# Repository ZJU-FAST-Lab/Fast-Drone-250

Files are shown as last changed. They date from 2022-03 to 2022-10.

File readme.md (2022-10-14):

<font size=6> **从零制作自主空中机器人** </font>

本文档是视频教程[从零制作自主空中机器人](https://www.bilibili.com/video/BV1WZ4y167me?p=1)的配套文档,github链接为https://github.com/ZJU-FAST-Lab/Fast-Drone-250

<font color="#dd0000">安全事项</font>

四旋翼无人机具有较高的安全风险，请同学们严格遵守安全规范，不要在有人的室内或室外进行试验，对自己和他人的安全负责，本实验室完全免责。

- [第一章：课程介绍](#第一章课程介绍)
- [第二章：动力套焊接](#第二章动力套焊接)
- [第三章：飞控的安装与接线](#第三章飞控的安装与接线)
- [第四章：飞控设置与试飞](#第四章飞控设置与试飞)
- [第五章：机载电脑与传感器的安装](#第五章机载电脑与传感器的安装)
- [第六章：Ubuntu20.04的安装](#第六章ubuntu2004的安装)
- [第七章：机载电脑的环境配置](#第七章机载电脑的环境配置)
- [第八章：常用实验与调试软件的安装与使用](#第八章常用实验与调试软件的安装与使用)
- [第九章：Ego-Planner代码框架与参数介绍](#第九章ego-planner代码框架与参数介绍)
- [第十章：VINS的参数设置与外参标定](#第十章vins的参数设置与外参标定)
- [第十一章：Ego-Planner的实验](#第十一章ego-planner的实验)
- [Q&A 常见问题及解答](#qa-常见问题及解答)

## 第一章：课程介绍
  本次课程是一套面向对自主空中机器人感兴趣的学生、爱好者、相关从业人员的免费课程，包含了从硬件组装、机载电脑环境设置、代码部署、实机实验等全套详细流程，带你从0开始，组装属于自己的自主无人机，并让它可以在未知的环境中自由避障穿行。本次课程所涉及的所有代码、硬件设计全部开源，<font color="#dd0000">严禁商用与转载，版权与最终解释权由浙江大学FASTLAB实验室所有。</font>
  本次课程的重心主要落在自主空中机器人的搭建、代码部署及调试上，关于自主空中机器人的一些理论基础，例如动力学模型，路径搜索，轨迹规划，地图构建等内容，高飞老师在深蓝学院有非常详尽而深入浅出的[课程](https://www.shenlanxueyuan.com/course/385?source=1)，本次课程就不再赘述。

## 第二章：动力套焊接
  机器人本体相关配件及焊接用工具详见[purchase_list.xlsx](purchase_list.xlsx),对硬件选型有相关疑问请看 番外一：硬件选型
## 第三章：飞控的安装与接线
* 一定要注意电调信号线顺序！！！
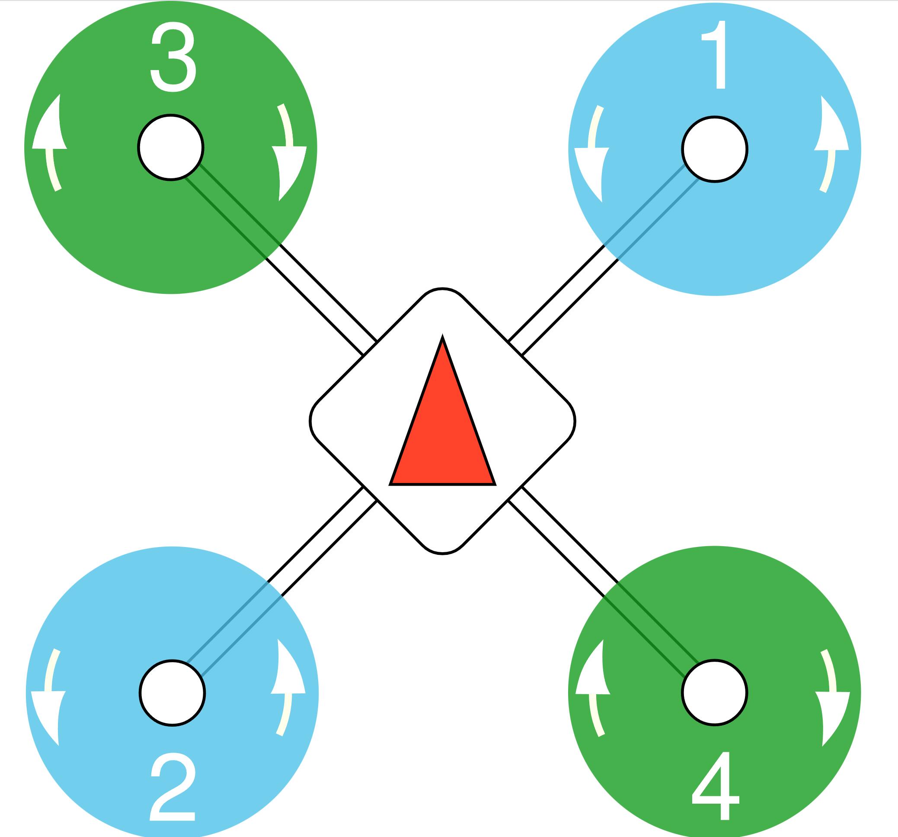
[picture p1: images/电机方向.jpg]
电机方向
  
* 飞控箭头与机头同向为正向，任意方向旋转90°的倍数也可以，后续可以在飞控设置内调整，推荐和视频内相同朝向摆放。
* <font color="#dd0000">强烈推荐使用硅胶杜邦线，常规杜邦线线材过硬，容易出现接触不良。</font>
* 5V稳压模块注意贴黑胶带绝缘，周围注意贴一圈厚的海绵胶带来防止飞机降落时损坏5V模块，也可以考虑把5V模块用扎带扎在机臂旁边
* 使用V5+飞控或其他把模拟和数字输出分开的飞控（特点是输出口标号为A1~A4 M1~M4），如果要用Dshot协议，请插在A口上

## 第四章：飞控设置与试飞

* 请烧录本git项目下的`/firmware/px4_fmu-v5_default.px4`固件，这个固件是官方1.11.0版本固件编译而来，如有需要可以自行编译。实测1.13版本固件存在BUG，不建议使用，更老的固件版本未经测试。

* 在飞控的sd卡的根目录下创建`/etc/extras.txt`，写入

  ```
  mavlink stream -d /dev/ttyACM0 -s ATTITUDE_QUATERNION -r 200
  mavlink stream -d /dev/ttyACM0 -s HIGHRES_IMU -r 200
  ```
  
  以提高imu发布频率
  
* 修改机架类型为 `Generic 250 Racer`，代指250mm轴距机型。如果是其他尺寸的机架，请根据实际轴距选择机架类型

* 修改`dshot_config`为dshot600

* 修改`CBRK_SUPPLY_CHK`为894281 *执行这步跳过了电源检查，因此左侧栏的电池设置部分就算是红的也没关系*

* 修改`CBRK_USB_CHK`为197848

* 修改`CBRK_IO_SAFETY`为22027

* 修改`SER_TEL1_BAUD`为921600

* 修改`SYS_USE_IO`为0（搜索不到则不用管）

* 上电前请先用万用表通断档检测电源正负焊点是否短接，强烈建议第一次上电前先接一个[短路保护器](https://item.taobao.com/item.htm?spm=a230r.1.14.6.72b83b20uNbZk7&id=656973651729&ns=1&abbucket=19#detail)

* <font color="#dd0000">检测电机转向前确保没有安装螺旋桨！！！！</font>

* 修改电机转向：进入mavlink控制台

  ```
  dshot reverse -m 1
  dshot save -m 1
  ```

  修改`1`为需要反向的电机序号
  
* <font color="#dd0000">第一次试飞请务必找有自稳模式下飞行经验的飞手协助，只飞过大疆无人机的飞手99%无法飞好！</font>

* 身边没有有经验的飞手怎么办？详见Q&A

## 第五章：机载电脑与传感器的安装

* 碳板已经预留了拆壳NUC的安装空位。如果想拆壳安装NUC，需要额外购买USB网卡，或者拆下自带的网卡天线找地方固定住，并且由于碳纤维板导电，请务必用尼龙柱把NUC支起来，相关资料请自行查阅。
* 机载电脑使用4S航模电池直接供电，正常情况下没有问题。但理论上最好接一个稳压模块，否则在无人机炸机/电池几乎耗尽时会出现机载电脑关机的情况。但由于符合NUC功率的稳压模块比较大，请同学们酌情选用。

## 第六章：Ubuntu20.04的安装

* 镜像站地址：`http://mirrors.aliyun.com/ubuntu-releases/20.04/` 下载 `ubuntu-20.04.4-desktop-amd64.iso`
* 烧录软件UltraISO官网：`https://cn.ultraiso.net/`
* 分区设置：
  * EFI系统分区（主分区）512M
  * 交换空间（逻辑分区）16000M（内存大小的两倍）
  * 挂载点`/`（主分区）剩余所有容量
  * <font color="#dd0000">笔记本上也需要安装ubuntu，推荐装20.04版本。虚拟机或双系统都可以，如果有长期学习打算推荐双系统</font>
## 第七章：机载电脑的环境配置

* ROS安装
  * `sudo sh -c 'echo "deb http://packages.ros.org/ros/ubuntu $(lsb_release -sc) main" > /etc/apt/sources.list.d/ros-latest.list'`
  * `sudo apt-key adv --keyserver 'hkp://keyserver.ubuntu.com:80' --recv-key C1CF6E31E6BADE8868B172B4F42ED6FBAB17C654`
  * `sudo apt update`
  * `sudo apt install ros-noetic-desktop-full`
  * `echo "source /opt/ros/noetic/setup.bash" >> ~/.bashrc`
  * <font color="#dd0000">建议没有ROS基础的同学先去B站学习古月老师的ROS入门教程</font>
* 测试ROS
  * 打开三个终端，分别输入
  * `roscore`
  * `rosrun turtlesim turtlesim_node`
  * `rosrun turtlesim turtle_teleop_key`
* realsense驱动安装
  * `sudo apt-key adv --keyserver keyserver.ubuntu.com --recv-key  F6E65AC044F831AC80A06380C8B3A55A6F3EFCDE || sudo apt-key adv --keyserver hkp://keyserver.ubuntu.com:80 --recv-key  F6E65AC044F831AC80A06380C8B3A55A6F3EFCDE`
  * `sudo add-apt-repository "deb https://librealsense.intel.com/Debian/apt-repo $(lsb_release -cs) main" -u`
  * `sudo apt-get install librealsense2-dkms`
  * `sudo apt-get install librealsense2-utils`
  * `sudo apt-get install librealsense2-dev`
  * `sudo apt-get install librealsense2-dbg`
  * 测试：`realsense-viewer`
  * <font color="#dd0000">注意测试时左上角显示的USB必须是3.x，如果是2.x，可能是USB线是2.0的，或者插在了2.0的USB口上（3.0的线和口都是蓝色的）</font>
* 安装mavros
  * `sudo apt-get install ros-noetic-mavros`
  * `cd /opt/ros/noetic/lib/mavros`
  * `sudo ./install_geographiclib_datasets.sh`
* 安装ceres与glog与ddyanmic-reconfigure
  * 解压`3rd_party.zip`压缩包
  * 进入glog文件夹打开终端
  * `./autogen.sh && ./configure && make && sudo make install`
  * `sudo apt-get install liblapack-dev libsuitesparse-dev libcxsparse3.1.2 libgflags-dev libgoogle-glog-dev libgtest-dev`
  * 进入ceres文件夹打开终端
  * `mkdir build`
  * `cd build`
  * `cmake ..`
  * `sudo make -j4`
  * `sudo make install`
  * `sudo apt-get install ros-noetic-ddynamic-reconfigure`
* 下载ego-planner源码并编译
  * `git clone https://github.com/ZJU-FAST-Lab/Fast-Drone-250`
  * `cd Fast-Drone-250`
  * `catkin_make`
  * `source devel/setup.bash`
  * `roslaunch ego_planner single_run_in_sim.launch`
  * 在Rviz内按下键盘G键，再单击鼠标左键以点选无人机目标点

## 第八章：常用实验与调试软件的安装与使用

* VScode：`sudo dpkg -i ***.deb`
* Terminator：`sudo apt install terminator`
* Plotjuggler：
  * `sudo apt install ros-noetic-plotjuggler`
  * `sudo apt install ros-noetic-plotjuggler-ros`
  * `rosrun plotjuggler plotjuggler`
* Net-tools：
  * `sudo apt install net-tools`
  * `ifconfig`
* ssh：
  * `sudo apt install openssh-server`
  * 在笔记本上：`ping 192.168.**.**`
  * `sudo gedit /etc/hosts`
  * 加上一行：`192.168.**.** fast-drone`
  * `ping fast-drone`
  * `ssh fast-drone@fast-drone`(`ssh 用户名@别名`)

## 第九章：Ego-Planner代码框架与参数介绍
* `src/planner/plan_manage/launch/single_run_in_exp.launch`下的：
  * `map_size`：当你的地图大小较大时需要修改，注意目标点不要超过map_size/2
  * `fx/fy/cx/cy`：修改为你的深度相机的实际内参（下一课有讲怎么看）
  * `max_vel/max_acc`：修改以调整最大速度、加速度。速度建议先用0.5试飞，最大不要超过2.5，加速度不要超过6
  * `flight_type`：1代表rviz选点模式，2代表waypoints跟踪模式
* `src/planner/plan_manage/launch/advanced_param_exp.xml`下的：
  * `resolution`：代表栅格地图格点的分辨率，单位为米。越小则地图越精细，但越占内存。最小不要低于0.1
  * `obstacles_inflation`：代表障碍物膨胀大小，单位为米。建议至少设置为飞机半径（包括螺旋桨、桨保）的1.5倍以上，但不要超过`resolution`的4倍。如果飞机轴距较大，请相应改大`resolution`
* `src/realflight_modules/px4ctrl/config/ctrl_param_fpv.yaml`下的：
  * `mass`：修改为无人机的实际重量
  * `hover_percent`：修改为无人机的悬停油门，可以通过px4log查看，具体可以参考[文档](https://www.bookstack.cn/read/px4-user-guide/zh-log-flight_review.md) 如果你的无人机是和课程的一模一样的话，这项保持为0.3即可。如果更改了动力配置，或重量发生变化，或轴距发生变化，都请调整此项，否则自动起飞时会发生无法起飞或者超调严重的情况。
  * `gain/Kp,Kv`：即PID中的PI项，一般不用太大改动。如果发生超调，请适当调小。如果无人机响应较慢，请适当调大。
  * `rc_reverse`：这项使用乐迪AT9S的不用管。如果在第十一课的自动起飞中，发现飞机的飞行方向与摇杆方向相反，说明需要修改此项，把相反的通道对应的值改为true。其中throttle如果反了，实际实验中会比较危险，建议在起飞前就确认好，步骤为：
    * `roslaunch mavros px4.launch`
    * `rostopic echo /mavros/rc/in`
    * 打开遥控器，把遥控器油门从最低满满打到最高
    * 看echo出来的消息里哪项在缓慢变化（这项就是油门通道值），并观察它是不是由小变大
    * 如果是由小变大，则不需要修改throttle的rc_reverse，反之改为true
    * 其他通道同理
  
## 第十章：VINS的参数设置与外参标定
* 检查飞控mavros连接正常
  * `ls /dev/tty*`，确认飞控的串口连接正常。一般是`/dev/ttyACM0`
  * `sudo chmod 777 /dev/ttyACM0`，为串口附加权限
  * `roslaunch mavros px4.launch`
  * `rostopic hz /mavros/imu/data_raw`，确认飞控传输的imu频率在200hz左右
* 检查realsense驱动正常
  * `roslaunch realsense2_camera rs_camera.launch`
  * 进入远程桌面，`rqt_image_view`
  * 查看`/camera/infra1/image_rect_raw`,`/camera/infra2/image_rect_raw`,`/camera/depth/image_rect_raw`话题正常
* VINS参数设置
  * 进入`realflight_modules/VINS_Fusion/config/`
  
  * 驱动realsense后，`rostopic echo /camera/infra1/camera_info`，把其中的K矩阵中的fx,fy,cx,cy填入`left.yaml`和`right.yaml`
  
  * 在home目录创建`vins_output`文件夹(如果你的用户名不是fast-drone，需要修改config内的vins_out_path为你实际创建的文件夹的绝对路径)
  
  * 修改`fast-drone-250.yaml`的`body_T_cam0`和`body_T_cam1`的`data`矩阵的第四列为你的无人机上的相机相对于飞控的实际外参，单位为米，顺序为x/y/z，第四项是1，不用改
  
* VINS外参精确自标定
  * `sh shfiles/rspx4.sh`
  * `rostopic echo /vins_fusion/imu_propagate`
  * 拿起飞机沿着场地<font color="#dd0000">尽量缓慢</font>地行走，场地内光照变化不要太大，灯光不要太暗，<font color="#dd0000">不要使用会频闪的光源</font>，尽量多放些杂物来增加VINS用于匹配的特征点
  * 把`vins_output/extrinsic_parameter.txt`里的内容替换到`fast-drone-250.yaml`的`body_T_cam0`和`body_T_cam1`
  * 重复上述操作直到走几圈后VINS的里程计数据偏差收敛到满意值（一般在0.3米内）
* 建图模块验证
  * `sh shfiles/rspx4.sh`
  * `roslaunch ego_planner single_run_in_exp.launch`
  * 进入远程桌面 `roslaunch ego_planner rviz.launch`

## 第十一章：Ego-Planner的实验
* 自动起飞：

  * `sh shfiles/rspx4.sh`
  * `rostopic echo /vins_fusion/imu_propagate`
  * 拿起飞机进行缓慢的小范围晃动，放回原地后确认没有太大误差
  * 遥控器5通道拨到内侧，六通道拨到下侧，油门打到中位
  * `roslaunch px4ctrl run_ctrl.launch`
  * `sh shfiles/takeoff.sh`，如果飞机螺旋桨开始旋转，但无法起飞，说明`hover_percent`参数过小；如果飞机有明显飞过1米高，再下降的样子，说明`hover_percent`参数过大
  * 遥控器此时可以以类似大疆飞机的操作逻辑对无人机进行位置控制
  * 降落时把油门打到最低，等无人机降到地上后，把5通道拨到中间，左手杆打到左下角上锁
* Ego-Planner实验
  * 自动起飞
  * `roslaunch ego_planner single_run_in_exp.launch`
  * `sh shfiles/record.sh`
  * 进入远程桌面 `roslaunch ego_planner rviz.launch`
  * 按下G键加鼠标左键点选目标点使无人机飞行
* <font color="#dd0000">如果实验中遇到意外怎么办！！！</font>
  * `case 1`: VINS定位没有飘，但是规划不及时/建图不准确导致无人机规划出一条可能撞进障碍物的轨迹。如果飞手在飞机飞行过程中发现无人机可能会撞到障碍物，在撞上前把6通道拨回上侧，此时无人机会退出轨迹跟随模式，进入VINS悬停模式，在此时把无人机安全着陆即可
  * `case 2`：VINS定位飘了，表现为飞机大幅度颤抖/明显没有沿着正常轨迹走/快速上升/快速下降等等，此时拨6通道已经无济于事，必须把5通道拨回中位，使无人机完全退出程序控制，回到遥控器的stablized模式来操控降落
  * `case 3`：无人机已经撞到障碍物，并且还没掉到地上。此时先拨6通道，看看飞机能不能稳住，稳不住就拨5通道手动降落
  * `case 4`：无人机撞到障碍物并且炸到地上了：拨5通道立刻上锁，减少财产损失
  * `case 5`：**绝招** 反应不过来哪种case，或者飞机冲着非常危险的区域飞了，直接拨7通道紧急停桨。这样飞机会直接失去动力摔下来，对飞机机身破坏比较大，一般慢速情况下不建议。

## Q&A 常见问题及解答

	Q: 能不能用265+435来不跑vins？
	A: 可以，但265直出的里程计的速度估计有问题，可能导致控制不稳定。需要把265和imu做ekf融合。
	
	Q: 硬件清单中的xxx能不能更换？
	A: 请看视频番外一，讲解了大部分替换可能。
	   如果要换大轴距机架，请相应更换动力套及桨叶。pid参数也需要相应调整，相关内容自行查阅。
	   435相机可以换430相机。430更便宜但没有外壳，不好固定且容易炸坏。
	   电池不建议更换，因为课程的Q250机架刚刚好可以塞入2300mah 4S电池，不需要额外固定。更换电池需要自行解决电池放置问题。
	
	Q: 能不能用D435i自带的imu运行vins?
	A: 不行，因为435的imu噪声很大
	
	Q: 课程提供的v1.11.0固件有什么改动吗？必须使用这个固件吗？
	A: 没有任何改动，是直接从px4官方下载的。目前仅在该版本上测试通过了本套代码，且在v1.13上测试失败，表现为VINS会经常崩溃。其他飞控/其他版本固件没有测试，有需要的同学可以自行测试。
	
	Q: QGC内测试电机不转怎么办？
	A: 1. 检查电调是否支持dshot，不支持请自行查阅pwm电调校准方法。 
	   2.如果是使用V5+飞控或其他把模拟和数字输出分开的飞控（特点是输出口标号为A1~A4 M1~M4），如果要用Dshot协议，请插在A口上
	   3.使用holybro pixhawk4完全版飞控，飞控与分电板的插线请插在FMU PWM OUTPUT上，而非I/O PWM OUTPUT
	
	Q: 运行vins后报红字错误？
	A: 大概率是你改config后格式错误，照着报错去修改对应的config
	
	Q: 运行vins后报"VINS_RESULT_PATH not opened"?
	A: 在home目录创建`vins_output`文件夹(如果你的用户名不是fast-drone，需要修改config内的vins_out_path为你实际创建的文件夹的绝对路径)
	
	Q: 这台飞机的载重有多少？续航有多少？能飞多远？
	A: 不带额外负载起飞重量在1.1~1.2kg左右，最大起飞重量在1.8kg内，再大控制不稳且续航很短。
		不带负载续航约5分钟。
		能飞多远取决于你wifi的通讯质量，一般wifi顶多通讯100米。此外由于栅格地图直接开在内存内，如果地图范围设置过大，容易占满内存导致其他程序运行缓慢。一般不建议超过50米*50米。
		
	Q: 为什么要挡住D435的结构光？
	A: 结构光的意义在于使相机得到的深度图更准确，但双目图片上会显示出位置固定不变的点阵光斑，这对VIO的运行是不利的，所以需要关掉。
	
	Q: VINS飘怎么办？
	A: 1. 检查环境中是否有强反光物体（瓷砖、玻璃等）
	   2. 尽量缓慢地移动无人机，场景内不要有运动物体
	   3. 尽量准确地测量初始外参
	   4. 不要在运行vins的时候在远程桌面上运行rviz（会占用大量CPU资源），实在想开建议去配一下ROS多机，然后在笔记本上开
	   5. 检查环境中是否有频闪光源（肉眼无法看出，在realsense的单目画面中检查）
	
	Q: 我没有自稳模式无人机的飞行经验，身边也没有有经验的飞手，怎么办呢？
	A: 1. 有预算的情况下，建议购买一台耐摔的带保护圈的穿越机来练手，推荐的型号有mobula6,吉朗小金鱼85x,化骨龙racewhoop30等
	   2. 没啥预算的情况下，建议购买一个遥控器加密狗来把课程推荐的AT9S遥控器连接到电脑，然后在模拟器里练熟。模拟器推荐steam上的liftoff,免费的推荐free rider
	
	Q: 我想用NX做机载电脑，该另外做些什么？
	A: 原则上不建议小白用NX，会多很多麻烦事，本课程并不涉及，助教也没有时间去帮你看。
	   需要额外做下面的事：
	   1. 修改VINS为GPU版本的，因为NX的CPU算力很差，跑课程的CPU版VINS一定跑不动
	   2. 解决NX固定及供电问题
	   3. 解决realsense固定问题
	   4. 解决NX用小底板时接口不够的问题
	   5. 解决一系列arm和x86不兼容带来的问题
	   
	Q: 我按照教程修改sd卡里的etc/extra.txt后，IMU频率没有变成200hz怎么办？
	A: 可能原因是你的固件不支持这样修改，可以尝试在启动mavros后执行：
	rosrun mavros mavcmd long 511 105 5000 0 0 0 0 0 & sleep 1;
	rosrun mavros mavcmd long 511 31 5000 0 0 0 0 0 & sleep 1;

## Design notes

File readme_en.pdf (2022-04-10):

# Build an autonomous aerial robot from scratch

This is a companion document to the video Build an autonomous aerial robot from scratch. (https://www.bilibili.com/video/BV1WZ4y167me?p=1) Operating aerial robots is risky! Please strictly abide by the safety regulations! ! !

Chapter 1: Course Introduction
Chapter 2: Drone Assembly
Chapter 3: Installation and wiring of flight controller
Chapter 4: Setup and flight test of flight controller
Chapter 5: Assembly of Onboard Computer and Sensors
Chapter 6: Installation of ubuntu20 04
Chapter 7: Environmental Configuration of the Airborne Computer
Chapter 8: Installation and Instructions of Experiment and Debugging Software Chapter 9: Instructions of Ego-Planner
Chapter 10: setting of VINS
Chapter 11: Experiments of Ego-Planner

# Chapter 1: Course Introduction

This course is a set of free courses for students, enthusiasts, and related practitioners who are interested in autonomous aerial robots. It includes a complete set of detailed procedures from hardware assembly, airborne computer environment setting, code deployment, and real machine experiments. Assemble your own autonomous drone from, and make it explore autonomously and keep away from obstacles in an unknown environment. All code and hardware design involved in this course are all open source,Commercial use and reprinting are strictly prohibited. The copyright and final interpretation rights are reserved by FAST-LAB, Zhejiang University.
The focus of this course is mainly on the assembly, code deployment and debugging of autonomous aerial robots. Some theoretical foundations of autonomous aerial robots, such as dynamic model, path search, trajectory planning, mapping, etc., are taught by Fei Gao in Shenlan College [course] (https://www.shenlanxueyuan.com/course/385?source=1), which will not be repeated in this course.

# Chapter 2: Drone Assembly

For details about the accessories and welding tools of the aerial body, please refer to purchase_list.xlsx. If you have any questions about hardware, please refer to Extra 1: Hardware Selection.

# Chapter 3: Installation and wiring of flight controller

Be sure to pay attention to the order of the ESC signal lines! ! !


If the arrow of the flight controller is in the same direction as the aircraft, the flight controller is forward. If rotating a multiple of 90° in any direction, you can also adjust the parameters in the flight control settings later. It is recommended to place the controller in the same orientation as in the video.
It is strongly recommended to use silicone DuPont wire. Conventional DuPont wire is too hard and is prone to poor contact.
Note that the surface of the 5V voltage regulator module should be covered with black tape for insulation. Stick a thick sponge tape around it to prevent damage to the 5V module when landing. You can also consider sticking it to the arm or else places.

# Chapter 4: Setup and flight test of flight controller

Please burn the firmware under this git project /firmware/px4_fmu-v5_default.px4 ，This firmware is compiled from the official v1.11.0 px4 firmware. You can compile it yourself if necessary. Firmware v1.13 is not suitable for this project. The older firmware version has not

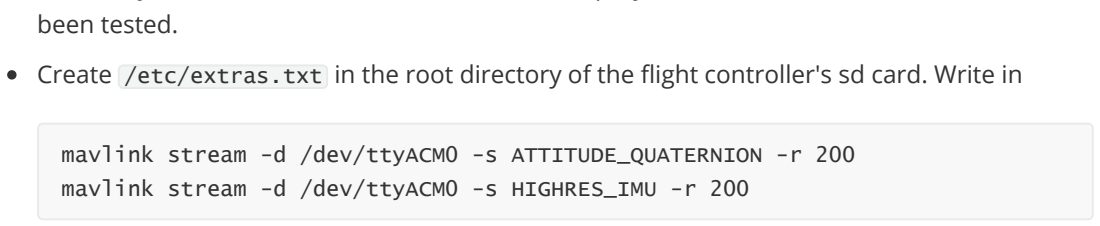
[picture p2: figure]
been tested.

Create /etc/extras.txt in the root directory of the flight controller's sd card. Write in

to increase the frequency of IMU.
Modify the Airframe to Generic 250 Racer ，Refers to the 250mm wheelbase model. Please select the type according to the actual wheelbase.
Modify the following parameters.

dshot_config : dshot600

CBRK_SUPPLY_CHK : 894281

CBRK_USB_CHK : 197848

CBRK_IO_SAFETY : 22027

SER_TEL1_BAUD : 921600
SYS_USE_IO : 0（No set if not found）
Make sure the propeller is not installed before checking the rotation of the motor! ! !

mavlink stream -d /dev/ttyACM0 -s ATTITUDE_QUATERNION -r 200 mavlink stream -d /dev/ttyACM0 -s HIGHRES_IMU -r 200

Modify the rotation direction of the motor. Enter the mavlink console.

1 is the number of the motor that needs to be reversed
For the first test flight, please be sure to seek the assistance of a pilot who has flying experience in the self-stabilizing mode. 99% of pilots who have only flown DJI cannot fly well!

# Chapter 5: Assembly of Onboard Computer and Sensors

The carbon plate has reserved the installation hole for NUC that has removed the shell . If you want to remove the shell, you need to buy an additional USB network card, or remove the network card antenna and find a place to fix it. Because the carbon fiber board is conductive, please be sure to support the NUC with nylon column.
The NUC uses the 4S aircraft battery to directly supply power, and there is no problem under normal circumstances. But it is better to connect a voltage stabilizing module. Please choose it as appropriate.

# Chapter 6: Installation of ubuntu20 04

Address of the mirror station： http://mirrors.aliyun.com/ubuntu-releases/20.04/ .

Download ubuntu-20.04.4-desktop-amd64.iso

UltraISO for burning： https://cn.ultraiso.net/
Disk Partitioning：
EFI 512M
swap area 16000M（twice the memory size）
mount point / all capacity remaining
Ubuntu also needs to be installed on the PC or notebook. It is recommended to install ubuntu 20.04 virtual machine or dual system. Dual system is better if there is a long-term learning plan

# Chapter 7: Environmental Configuration of the Airborne Computer

ROS installation

sudo sh -c 'echo "deb http://packages.ros.org/ros/ubuntu $(lsb_release -sc)

main" > /etc/apt/sources.list.d/ros-latest.list'

sudo apt-key adv --keyserver 'hkp://keyserver.ubuntu.com:80' --recv-key

C1CF6E31E6BADE8868B172B4F42ED6FBAB17C654'

sudo apt update
sudo apt install ros-noetic-desktop-full

echo "source /opt/ros/noetic/setup.bash" >> ~/.bashrc
It is recommended that students who do not know ROS first learn the ROS introductory tutorial by Guyueju in Bilibili.
ROS test
Open three terminals and enter

roscore

dshot reverse -m 1
dshot save -m 1

sudo apt-key adv --keyserver keyserver.ubuntu.com --recv-key

F6E65AC044F831AC80A06380C8B3A55A6F3EFCDE || sudo apt-key adv --keyserver

hkp://keyserver.ubuntu.com:80 --recv-key

F6E65AC044F831AC80A06380C8B3A55A6F3EFCDE
sudo add-apt-repository "deb https://librealsense.intel.com/Debian/apt-repo

$(lsb_release -cs) main" -u

sudo apt-get install librealsense2-dkms

sudo apt-get install librealsense2-utils

sudo apt-get install librealsense2-dev

sudo apt-get install librealsense2-dbg
test： realsense-viewer
Note that the connected USB port must be 3.x (blue). mavros installation

sudo apt-get install ros-noetic-mavros

cd /opt/ros/noetic/lib/mavros

sudo ./install_geographiclib_datasets.sh
installation of ceres, glog and ddyanmic-reconfigure

unzip 3rd_party.zip
Open the terminal and enter the ./glog

./autogen.sh && ./configure && make && sudo make install
sudo apt-get install liblapack-dev libsuitesparse-dev libcxsparse3.1.2

libgflags-dev libgoogle-glog-dev libgtest-dev
Open the terminal and enter the ./ceres

mkdir build

cd build

cmake ..
sudo make -j4

sudo make install
sudo apt-get install ros-noetic-ddynamic-reconfigure
Download ego-planner code and compile

git clone https://github.com/ZJU-FAST-Lab/Fast-Drone-250

cd Fast-Drone-250

catkin_make

source devel/setup.bash

roslaunch ego_planner single_run_in_sim.launch
Press the G key on the keyboard in Rviz, then click the left button of mouse to select the target point of the drone

# Chapter 8: Installation and Instructions of Experiment and Debugging Software

VScode： sudo dpkg --i ***.deb

Terminator： sudo apt install terminator
Plotjuggler：

sudo apt install ros-noetic-plotjuggler

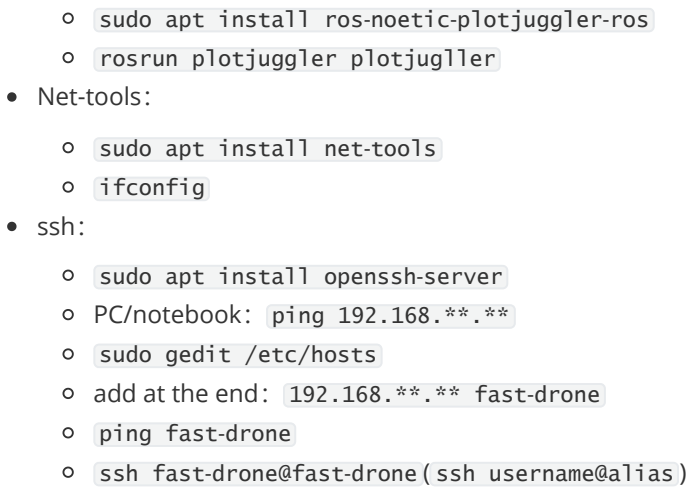
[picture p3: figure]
sudo apt install ros-noetic-plotjuggler-ros; rosrun plotjuggler plotjugller Net-tools：; sudo apt install net-tools; ifconfig ssh：; sudo apt install openssh-server; PC/notebook： ping 192.168.**.**; sudo gedit /etc/hosts; ping fast-drone

add at the end： 192.168.**.** fast-drone

ssh fast-drone@fast-drone ( ssh username@alias )

# Chapter 9: Instructions of Ego-Planner

src/planner/plan_manage/launch/single_run_in_exp.launch ：
map_size ：When your map is large, it needs to be modified. Note that the target point should not exceed the map_ size/2
fx/fy/cx/cy ：Actual internal parameters of your depth camera
max_vel/max_acc ：Max speed and acceleration. It is recommended to use 0.5 for test first. The maximum speed should not exceed 2.5. The acceleration should not exceed 6 flight_type ：1 represents rviz point selection mode, 2 represents waypoints tracking mode.
src/planner/plan_manage/launch/advanced_param_exp.xml 下的：
resolution ：Represents the resolution of the grid points of the raster map, in meters. The smaller the map, the finer the map, but the more memory it takes up. The
minimum should not be lower than 0.1
obstacles_inflation ：Represents the expansion size of the obstacle, in meters. It is recommended to set at least 1.5 times the radius of the aircraft (including the propeller), but not more than 4 times the resolution . If the wheelbase of the aircraft is larger, please increase the resolution

src/realflight_modules/px4ctrl/config/ctrl_param_fpv.yaml ：
mass ：Actual weight of the drone
hover_percent ：The hovering throttle of the drone. It can be viewed through px4log. For details, please refer to document (https://www.bookstack.cn/read/px4-user-guide/zh-log-flight_review.md) If your drone is exactly the same as the course, keep this at 0.3. If the power configuration, or the weight, or the wheelbase is changed, please adjust this item. Otherwise the automatic takeoff will fail to take off or the overshoot will be serious.
gain/Kp,Kv ：PID's P and I. Generally, no major changes are required. If overshoot occurs, please adjust it appropriately. If the drone is slow to respond, please adjust it appropriately
rc_reverse ：No changes required if using AT9S。If it is found that the flight direction of the aircraft is opposite to the direction of the joystick, it is necessary to modify this item. Change the value corresponding to the opposite channel to true . If the throttle is reversed, the experiment will be very dangerous. It is recommended to confirm it before taking off：

roslaunch mavros px4.launch

rostopic echo /mavros/rc/in

Turn on the remote control and turn the remote control throttle from the lowest to the highest
See which item in the echo message is changing slowly (this item is the throttle channel value) and observe whether it changes from small to large
If it changes from small to large, there is no need to modify the rc_reverse of the throttle, otherwise change to true
The same for other channels

# Chapter 10: setting of VINS

Check the connection is normal
ls /dev/tty* ，confirm that the serial port connection of the flight controller is normal. Generally is /dev/ttyACM0
sudo chmod 777 /dev/ttyACM0 ，give serial port permissions

roslaunch mavros px4.launch
rostopic hz /mavros/imu/data_raw ，confirm that the imu frequency transmitted by the flight control is around 200hz
Check that the realsense driver is normal

roslaunch realsense2_camera rs_camera.launch
Enter remote desktop, rqt_image_view
Check
/camera/infra1/image_rect_raw , /camera/infra2/image_rect_raw , /camera/depth/

image_rect_raw is normal
VINS parameter settings

Check realflight_modules/VINS_Fusion/config/

Drive realsense， rostopic echo /camera/infra1/camera_info ，fill in left.yaml
and right.yaml with fx, fy, cx, cy in the K matrix
Create a vins_output folder in the home directory

Modify in fast-drone-250.yaml , for body_T_cam0 and body_T_cam1 , data 's fourth
column to the actual extrinsic parameters of the camera on your drone relative to the flight control，in meters. The order is x/y/z, the fourth item is 1, no need to change Accurate self-calibration of VINS external parameters

sh shfiles/rspx4.sh

rostopic echo /vins_fusion/imu_propagate
Pick up the robot and walk slowlyin the field. The lighting in the venue should not change too much.Do not use light sources that flicker. Put as many clutter as possible to increase the feature points that VINS uses for matching
Replace the content in vins_output/extrinsic_parameter.txt to body_T_cam0 and

body_T_cam1 of fast-drone-250.yaml
Repeat the above operation until the odometer data deviation of VINS converges to a satisfactory value after a few laps (usually within 0.3 meters)
Test of mapping

sh shfiles/rspx4.sh

roslaunch ego_planner single_run_in_exp.launch Enter remote desktop, roslaunch ego_planner rviz.launch

# Chapter 11: Experiments of Ego-Planner

Automatic takeoff

sh shfiles/rspx4.sh

rostopic echo /vins_fusion/imu_propagate
Pick up the robot and remove it slowly in a small range. After putting it back in place, make sure VINS in a small deviation.
Channel 5 of the RC is dialed to the inside. Channel 6 is dialed to the lower side. The throttle is set to center.

roslaunch px4ctrl run_ctrl.launch
sh shfiles/takeoff.sh , If the propeller of the aircraft starts to rotate, but cannot take off, the hover_percent is too small. If the aircraft flies over 1 meter before descending, the hover_percent parameter is too big.
You can control the position of the drone, just like controlling the DJI
When landing, hit the throttle to the lowest level. After the drone is on the ground, set the channel 5 to the middle, and hit the left stick to the lower left corner to lock it. Experiment
Automatic takeoff

roslaunch ego-planner single_run_in_exp.launch

sh shfiles/record.sh
Enter remote desktop, roslaunch ego_planner rviz.launch
Press the G key and the left mouse button to click the target point to make the drone fly What to do if you encounter an accident during the experiment! ! !
case 1 : There is no problem with VINS positioning, but the untimely planning/inaccurate mapping causes the drone to plan a trajectory that may crash into an obstacle. If the pilot finds that the drone may hit an obstacle during the flight, turn the channel 6 back to the upper side before the collision. The drone will exit the trajectory following mode and enter the VINS hovering mode. Then land the drone safely
case 2 : VINS positioning inaccurately，It is manifested as a large tremor of the aircraft/obviously not following the normal trajectory or fast ascent or rapid descent, etc. At this time, it is useless to dial channel 6. You must turn channel 5 back to the middle position. Make the robot completely exit the program control and return to the stabilized mode of the RC. Then land
case 3 : The drone has hit an obstacle and hasn't fallen to the ground yet. At this time, dial channel 6 to see if the plane can stabilize. If not, dial channel 5 to land manually case 4 : The drone hit an obstacle and exploded to the ground. Dial channel 5 to lock it immediately to reduce property damage
case 5 : last resort If you can't figure out what kind of case, or the plane is flying towards a very dangerous area, dial channel 7 to stop the propellers directly. In this way, the aircraft will directly lose power and fall down, which will cause great damage to the fuselage of the aircraft. Generally, it is not recommended under slow speed conditions.

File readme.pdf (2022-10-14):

# 从零制作自主空中机器人

本文档是视频教程从零制作自主空中机器人 (https://www.bilibili.com/video/BV1WZ4y167me?p=1)的配套文档,github链接为https://github.com/ZJU-FAST-La

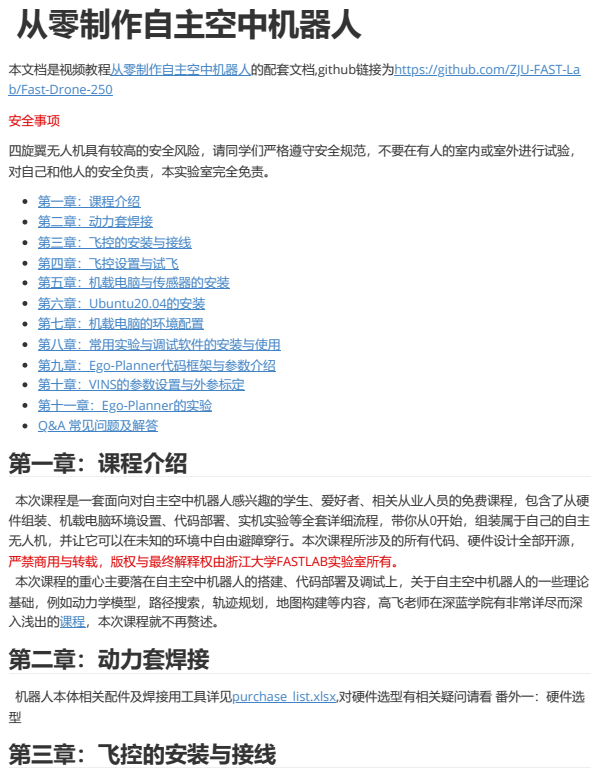
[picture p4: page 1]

b/Fast-Drone-250 (https://github.com/ZJU-FAST-Lab/Fast-Drone-250)
安全事项
四旋翼无人机具有较高的安全风险，请同学们严格遵守安全规范，不要在有人的室内或室外进行试验，
对自己和他人的安全负责，本实验室完全免责。
第一章：课程介绍
第二章：动力套焊接
第三章：飞控的安装与接线
第四章：飞控设置与试飞
第五章：机载电脑与传感器的安装
第六章：Ubuntu20.04的安装
第七章：机载电脑的环境配置
第八章：常用实验与调试软件的安装与使用
第九章：Ego-Planner代码框架与参数介绍
第十章：VINS的参数设置与外参标定
第十一章：Ego-Planner的实验
Q&A 常见问题及解答

本次课程是一套面向对自主空中机器人感兴趣的学生、爱好者、相关从业人员的免费课程，包含了从硬
件组装、机载电脑环境设置、代码部署、实机实验等全套详细流程，带你从0开始，组装属于自己的自主
无人机，并让它可以在未知的环境中自由避障穿行。本次课程所涉及的所有代码、硬件设计全部开源，
严禁商用与转载，版权与最终解释权由浙江大学FASTLAB实验室所有。
本次课程的重心主要落在自主空中机器人的搭建、代码部署及调试上，关于自主空中机器人的一些理论
基础，例如动力学模型，路径搜索，轨迹规划，地图构建等内容，高飞老师在深蓝学院有非常详尽而深
入浅出的课程，本次课程就不再赘述。 (https://www.shenlanxueyuan.com/course/385?source=1)

机器人本体相关配件及焊接用工具详见purchase_list.xlsx,对硬件选型有相关疑问请看 番外一：硬件选

## 一定要注意电调信号线顺序！！！

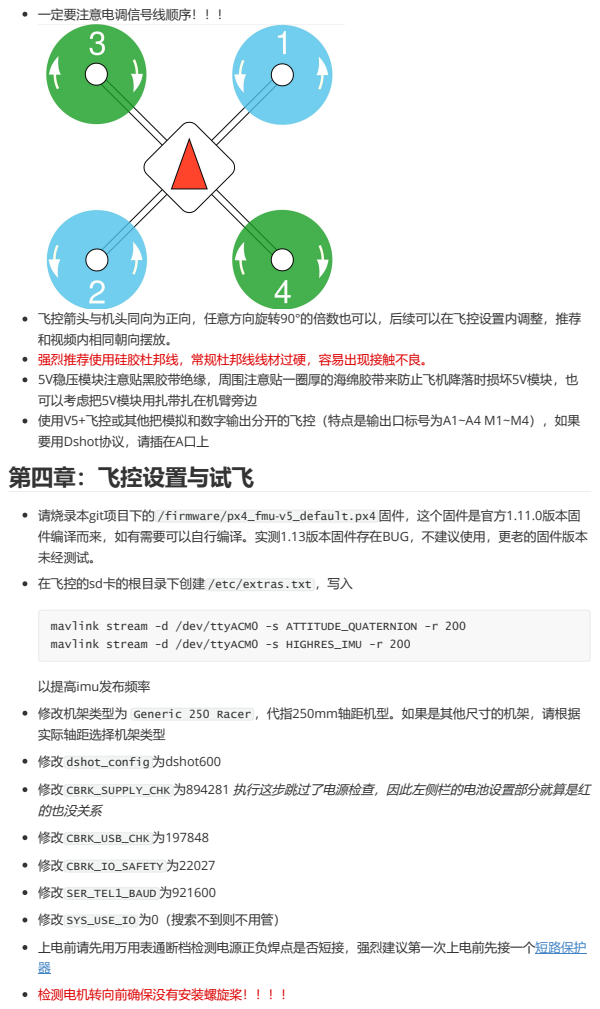
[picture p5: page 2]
修改 CBRK_USB_CHK 为197848; 修改 CBRK_IO_SAFETY 为22027; 修改 SER_TEL1_BAUD 为921600; 修改 SYS_USE_IO 为0（搜索不到则不用管）; 上电前请先用万用表通断档检测电源正负焊点是否短接，强烈建议第一次上电前先接一个短路保护 器; 检测电机转向前确保没有安装螺旋桨！！！！

飞控箭头与机头同向为正向，任意方向旋转90°的倍数也可以，后续可以在飞控设置内调整，推荐
和视频内相同朝向摆放。
强烈推荐使用硅胶杜邦线，常规杜邦线线材过硬，容易出现接触不良。
5V稳压模块注意贴黑胶带绝缘，周围注意贴一圈厚的海绵胶带来防止飞机降落时损坏5V模块，也
可以考虑把5V模块用扎带扎在机臂旁边
使用V5+飞控或其他把模拟和数字输出分开的飞控（特点是输出口标号为A1~A4 M1~M4），如果
要用Dshot协议，请插在A口上
第四章：飞控设置与试飞

请烧录本git项目下的 /firmware/px4_fmu-v5_default.px4 固件，这个固件是官方1.11.0版本固
件编译而来，如有需要可以自行编译。实测1.13版本固件存在BUG，不建议使用，更老的固件版本
未经测试。
在飞控的sd卡的根目录下创建 /etc/extras.txt ，写入

mavlink stream -d /dev/ttyACM0 -s ATTITUDE_QUATERNION -r 200
mavlink stream -d /dev/ttyACM0 -s HIGHRES_IMU -r 200

以提高imu发布频率
修改机架类型为 Generic 250 Racer ，代指250mm轴距机型。如果是其他尺寸的机架，请根据
实际轴距选择机架类型

修改 dshot_config 为dshot600
修改 CBRK_SUPPLY_CHK 为894281 执行这步跳过了电源检查，因此左侧栏的电池设置部分就算是红
的也没关系

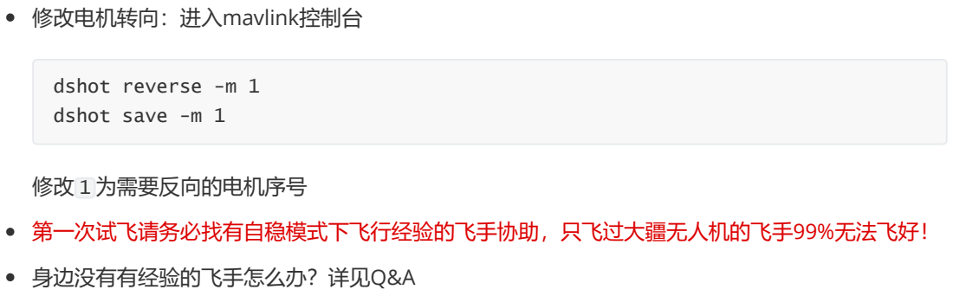
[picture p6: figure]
修改电机转向：进入mavlink控制台; 修改 1 为需要反向的电机序号; 身边没有有经验的飞手怎么办？详见Q&A; dshot reverse -m 1; dshot save -m 1

## 第一次试飞请务必找有自稳模式下飞行经验的飞手协助，只飞过大疆无人机的飞手99%无法飞好！

# 第五章：机载电脑与传感器的安装

## 碳板已经预留了拆壳NUC的安装空位。如果想拆壳安装NUC，需要额外购买USB网卡，或者拆下自 带的网卡天线找地方固定住，并且由于碳纤维板导电，请务必用尼龙柱把NUC支起来，相关资料请 自行查阅。 机载电脑使用4S航模电池直接供电，正常情况下没有问题。但理论上最好接一个稳压模块，否则在 无人机炸机/电池几乎耗尽时会出现机载电脑关机的情况。但由于符合NUC功率的稳压模块比较 大，请同学们酌情选用。

# 第六章：Ubuntu20.04的安装

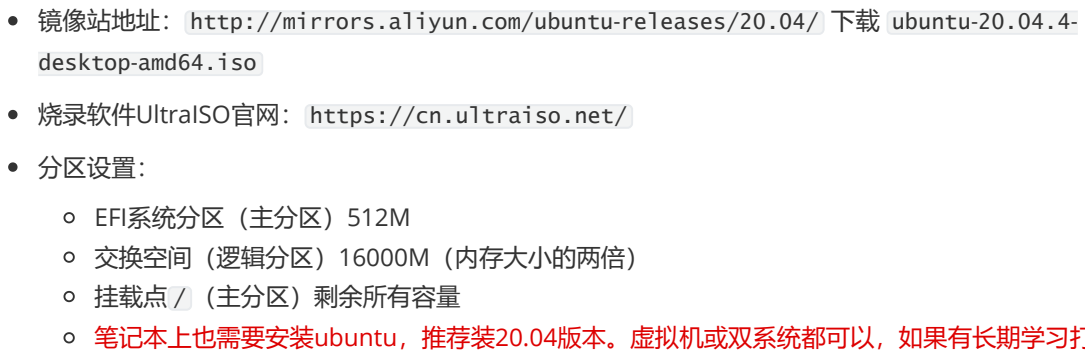
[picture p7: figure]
镜像站地址： http://mirrors.aliyun.com/ubuntu-releases/20.04/ 下载; ubuntu-20.04.4-; desktop-amd64.iso; 烧录软件UltraISO官网： https://cn.ultraiso.net/; 分区设置：; EFI系统分区（主分区）512M 交换空间（逻辑分区）16000M（内存大小的两倍） 挂载点 / （主分区）剩余所有容量

## 笔记本上也需要安装ubuntu，推荐装20.04版本。虚拟机或双系统都可以，如果有长期学习打 算推荐双系统

# 第七章：机载电脑的环境配置

## ROS安装

sudo sh -c 'echo "deb http://packages.ros.org/ros/ubuntu $(lsb_release -sc)

main" > /etc/apt/sources.list.d/ros-latest.list'

sudo apt-key adv --keyserver 'hkp://keyserver.ubuntu.com:80' --recv-key

C1CF6E31E6BADE8868B172B4F42ED6FBAB17C654

sudo apt update
sudo apt install ros-noetic-desktop-full

echo "source /opt/ros/noetic/setup.bash" >> ~/.bashrc

## 建议没有ROS基础的同学先去B站学习古月老师的ROS入门教程

## 测试ROS

## 打开三个终端，分别输入

roscore

rosrun turtlesim turtlesim_node

rosrun turtlesim turtle_teleop_key

## realsense驱动安装

sudo apt-key adv --keyserver keyserver.ubuntu.com --recv-key

F6E65AC044F831AC80A06380C8B3A55A6F3EFCDE || sudo apt-key adv --keyserver

hkp://keyserver.ubuntu.com:80 --recv-key

F6E65AC044F831AC80A06380C8B3A55A6F3EFCDE
sudo add-apt-repository "deb https://librealsense.intel.com/Debian/apt-repo

$(lsb_release -cs) main" -u

sudo apt-get install librealsense2-dkms

sudo apt-get install librealsense2-utils

sudo apt-get install librealsense2-dev

sudo apt-get install librealsense2-dbg
测试： realsense-viewer

## 注意测试时左上角显示的USB必须是3.x，如果是2.x，可能是USB线是2.0的，或者插在了2.0 的USB口上（3.0的线和口都是蓝色的）

## 安装mavros

sudo apt-get install ros-noetic-mavros

cd /opt/ros/noetic/lib/mavros

sudo ./install_geographiclib_datasets.sh

## 安装ceres与glog与ddyanmic-reconfigure

解压 3rd_party.zip 压缩包

## 进入glog文件夹打开终端

./autogen.sh && ./configure && make && sudo make install
sudo apt-get install liblapack-dev libsuitesparse-dev libcxsparse3.1.2

libgflags-dev libgoogle-glog-dev libgtest-dev

## 进入ceres文件夹打开终端

mkdir build

cd build

cmake ..
sudo make -j4

sudo make install
sudo apt-get install ros-noetic-ddynamic-reconfigure

## 下载ego-planner源码并编译

git clone https://github.com/ZJU-FAST-Lab/Fast-Drone-250

cd Fast-Drone-250

catkin_make

source devel/setup.bash

roslaunch ego_planner single_run_in_sim.launch

## 在Rviz内按下键盘G键，再单击鼠标左键以点选无人机目标点

# 第八章：常用实验与调试软件的安装与使用

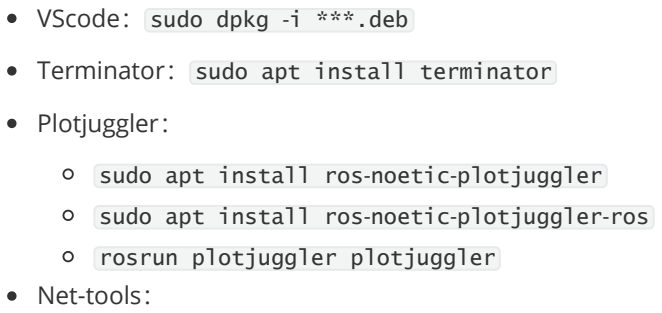
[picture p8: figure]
VScode： sudo dpkg -i ***.deb; Terminator： sudo apt install terminator; Plotjuggler：; sudo apt install ros-noetic-plotjuggler; sudo apt install ros-noetic-plotjuggler-ros; rosrun plotjuggler plotjuggler Net-tools：

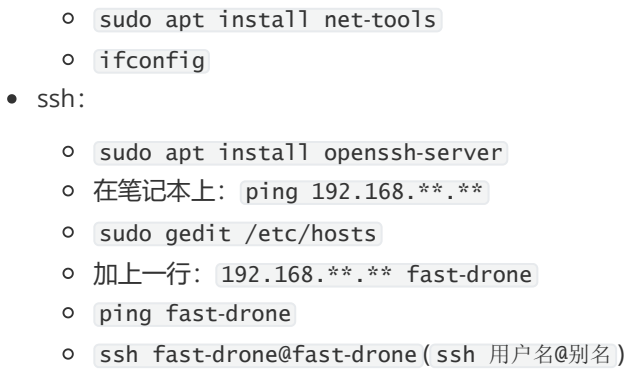
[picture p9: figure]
sudo apt install net-tools; ifconfig ssh：; sudo apt install openssh-server; 在笔记本上： ping 192.168.**.**; sudo gedit /etc/hosts 加上一行： 192.168.**.** fast-drone; ping fast-drone

ssh fast-drone@fast-drone ( ssh 用户名@别名 )

# 第九章：Ego-Planner代码框架与参数介绍

src/planner/plan_manage/launch/single_run_in_exp.launch 下的：

## map_size ：当你的地图大小较大时需要修改，注意目标点不要超过map_size/2 fx/fy/cx/cy ：修改为你的深度相机的实际内参（下一课有讲怎么看） max_vel/max_acc ：修改以调整最大速度、加速度。速度建议先用0.5试飞，最大不要超过 2.5，加速度不要超过6

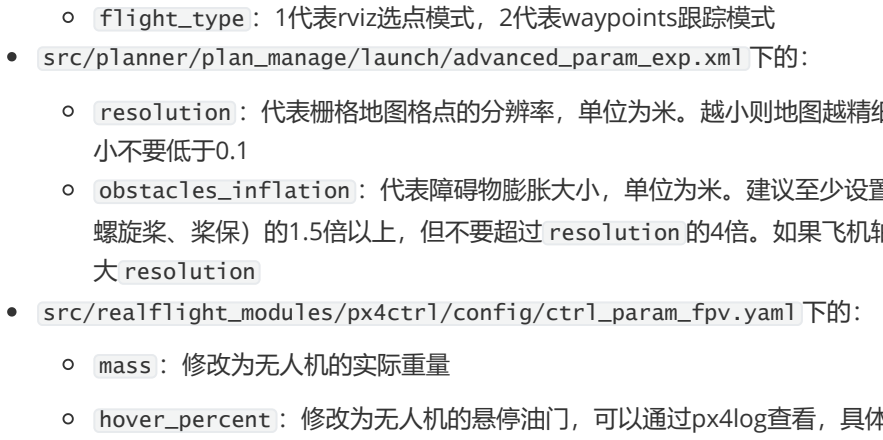
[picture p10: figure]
src/planner/plan_manage/launch/advanced_param_exp.xml 下的：; 小不要低于0.1; 大 resolution; src/realflight_modules/px4ctrl/config/ctrl_param_fpv.yaml 下的：; mass ：修改为无人机的实际重量

## flight_type ：1代表rviz选点模式，2代表waypoints跟踪模式

## resolution ：代表栅格地图格点的分辨率，单位为米。越小则地图越精细，但越占内存。最

## obstacles_inflation ：代表障碍物膨胀大小，单位为米。建议至少设置为飞机半径（包括 螺旋桨、桨保）的1.5倍以上，但不要超过 resolution 的4倍。如果飞机轴距较大，请相应改

hover_percent ：修改为无人机的悬停油门，可以通过px4log查看，具体可以参考文档 (https://www.bookstack.cn/read/px4-user-guide/zh-log-flight_review.md) 如果

## 你的无人机是和课程的一模一样的话，这项保持为0.3即可。如果更改了动力配置，或重量发 生变化，或轴距发生变化，都请调整此项，否则自动起飞时会发生无法起飞或者超调严重的情

况。

## gain/Kp,Kv ：即PID中的PI项，一般不用太大改动。如果发生超调，请适当调小。如果无人 机响应较慢，请适当调大。

## rc_reverse ：这项使用乐迪AT9S的不用管。如果在第十一课的自动起飞中，发现飞机的飞 行方向与摇杆方向相反，说明需要修改此项，把相反的通道对应的值改为true。其中throttle 如果反了，实际实验中会比较危险，建议在起飞前就确认好，步骤为：

roslaunch mavros px4.launch

rostopic echo /mavros/rc/in

## 打开遥控器，把遥控器油门从最低满满打到最高 看echo出来的消息里哪项在缓慢变化（这项就是油门通道值），并观察它是不是由小变

大

## 如果是由小变大，则不需要修改throttle的rc_reverse，反之改为true

## 其他通道同理

# 第十章：VINS的参数设置与外参标定

## 检查飞控mavros连接正常

ls /dev/tty* ，确认飞控的串口连接正常。一般是 /dev/ttyACM0

## 检查realsense驱动正常

查

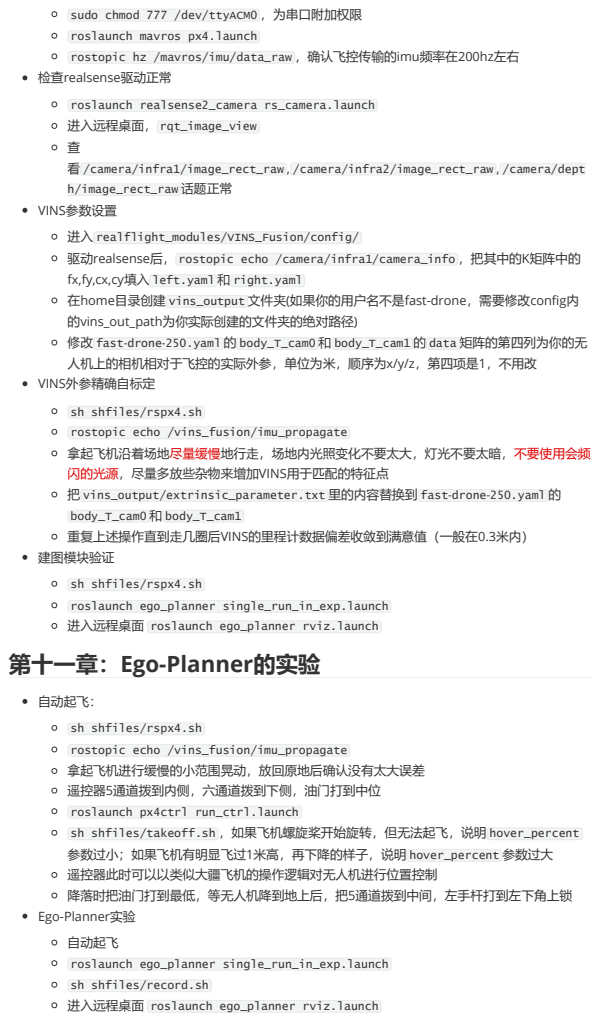
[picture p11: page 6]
roslaunch realsense2_camera rs_camera.launch 进入远程桌面， rqt_image_view; 自动起飞：

sudo chmod 777 /dev/ttyACM0 ，为串口附加权限

roslaunch mavros px4.launch
rostopic hz /mavros/imu/data_raw ，确认飞控传输的imu频率在200hz左右

看 /camera/infra1/image_rect_raw , /camera/infra2/image_rect_raw , /camera/dept
h/image_rect_raw 话题正常
VINS参数设置

进入 realflight_modules/VINS_Fusion/config/
驱动realsense后， rostopic echo /camera/infra1/camera_info ，把其中的K矩阵中的
fx,fy,cx,cy填入 left.yaml 和 right.yaml
在home目录创建 vins_output 文件夹(如果你的用户名不是fast-drone，需要修改config内
的vins_out_path为你实际创建的文件夹的绝对路径)
修改 fast-drone-250.yaml 的 body_T_cam0 和 body_T_cam1 的 data 矩阵的第四列为你的无
人机上的相机相对于飞控的实际外参，单位为米，顺序为x/y/z，第四项是1，不用改
VINS外参精确自标定

sh shfiles/rspx4.sh
rostopic echo /vins_fusion/imu_propagate
拿起飞机沿着场地尽量缓慢地行走，场地内光照变化不要太大，灯光不要太暗，不要使用会频
闪的光源，尽量多放些杂物来增加VINS用于匹配的特征点
把 vins_output/extrinsic_parameter.txt 里的内容替换到 fast-drone-250.yaml 的
body_T_cam0 和 body_T_cam1
重复上述操作直到走几圈后VINS的里程计数据偏差收敛到满意值（一般在0.3米内）
建图模块验证

roslaunch ego_planner single_run_in_exp.launch
进入远程桌面 roslaunch ego_planner rviz.launch
第十一章：Ego-Planner的实验

拿起飞机进行缓慢的小范围晃动，放回原地后确认没有太大误差
遥控器5通道拨到内侧，六通道拨到下侧，油门打到中位

roslaunch px4ctrl run_ctrl.launch
sh shfiles/takeoff.sh ，如果飞机螺旋桨开始旋转，但无法起飞，说明 hover_percent
参数过小；如果飞机有明显飞过1米高，再下降的样子，说明 hover_percent 参数过大
遥控器此时可以以类似大疆飞机的操作逻辑对无人机进行位置控制
降落时把油门打到最低，等无人机降到地上后，把5通道拨到中间，左手杆打到左下角上锁
Ego-Planner实验
自动起飞

sh shfiles/record.sh

## 按下G键加鼠标左键点选目标点使无人机飞行 如果实验中遇到意外怎么办！！！

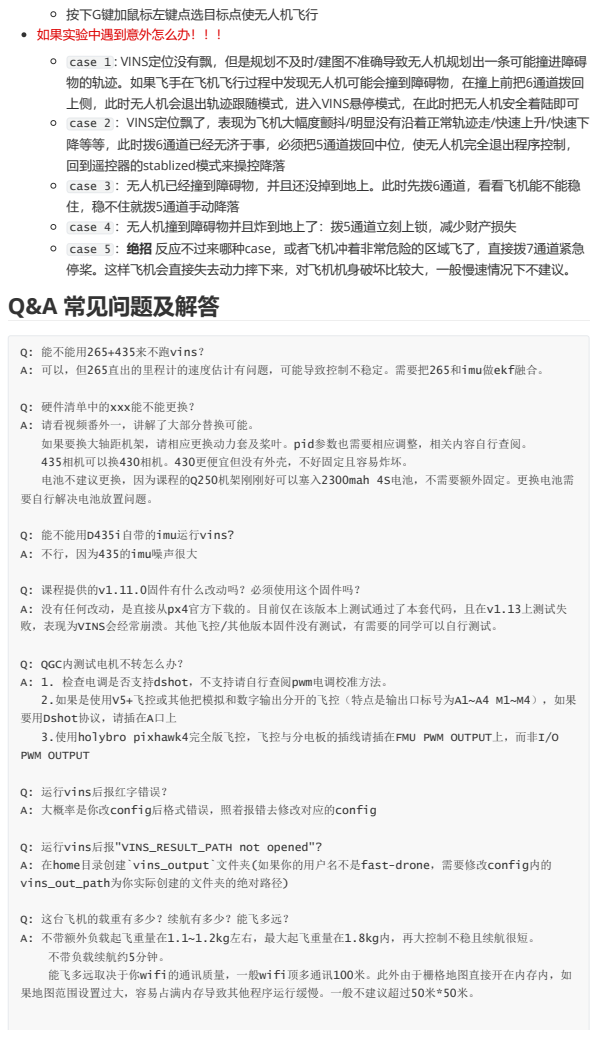
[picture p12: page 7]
Q: 能不能用265+435来不跑vins？; A: 可以，但265直出的里程计的速度估计有问题，可能导致控制不稳定。需要把265和imu做ekf融合。; Q: 能不能用D435i自带的imu运行vins?; A: 不行，因为435的imu噪声很大; Q: 运行vins后报红字错误？; A: 大概率是你改config后格式错误，照着报错去修改对应的config

case 1 : VINS定位没有飘，但是规划不及时/建图不准确导致无人机规划出一条可能撞进障碍
物的轨迹。如果飞手在飞机飞行过程中发现无人机可能会撞到障碍物，在撞上前把6通道拨回
上侧，此时无人机会退出轨迹跟随模式，进入VINS悬停模式，在此时把无人机安全着陆即可
case 2 ：VINS定位飘了，表现为飞机大幅度颤抖/明显没有沿着正常轨迹走/快速上升/快速下
降等等，此时拨6通道已经无济于事，必须把5通道拨回中位，使无人机完全退出程序控制，
回到遥控器的stablized模式来操控降落
case 3 ：无人机已经撞到障碍物，并且还没掉到地上。此时先拨6通道，看看飞机能不能稳
住，稳不住就拨5通道手动降落
case 4 ：无人机撞到障碍物并且炸到地上了：拨5通道立刻上锁，减少财产损失
case 5 ：绝招 反应不过来哪种case，或者飞机冲着非常危险的区域飞了，直接拨7通道紧急
停桨。这样飞机会直接失去动力摔下来，对飞机机身破坏比较大，一般慢速情况下不建议。
Q&A 常见问题及解答

Q: 硬件清单中的xxx能不能更换？
A: 请看视频番外一，讲解了大部分替换可能。
如果要换大轴距机架，请相应更换动力套及桨叶。pid参数也需要相应调整，相关内容自行查阅。
435相机可以换430相机。430更便宜但没有外壳，不好固定且容易炸坏。
电池不建议更换，因为课程的Q250机架刚刚好可以塞入2300mah 4S电池，不需要额外固定。更换电池需
要自行解决电池放置问题。

Q: 课程提供的v1.11.0固件有什么改动吗？必须使用这个固件吗？
A: 没有任何改动，是直接从px4官方下载的。目前仅在该版本上测试通过了本套代码，且在v1.13上测试失
败，表现为VINS会经常崩溃。其他飞控/其他版本固件没有测试，有需要的同学可以自行测试。

Q: QGC内测试电机不转怎么办？
A: 1. 检查电调是否支持dshot，不支持请自行查阅pwm电调校准方法。
2.如果是使用V5+飞控或其他把模拟和数字输出分开的飞控（特点是输出口标号为A1~A4 M1~M4），如果
要用Dshot协议，请插在A口上
3.使用holybro pixhawk4完全版飞控，飞控与分电板的插线请插在FMU PWM OUTPUT上，而非I/O
PWM OUTPUT

Q: 运行vins后报"VINS_RESULT_PATH not opened"?
A: 在home目录创建`vins_output`文件夹(如果你的用户名不是fast-drone，需要修改config内的
vins_out_path为你实际创建的文件夹的绝对路径)

Q: 这台飞机的载重有多少？续航有多少？能飞多远？
A: 不带额外负载起飞重量在1.1~1.2kg左右，最大起飞重量在1.8kg内，再大控制不稳且续航很短。
不带负载续航约5分钟。
能飞多远取决于你wifi的通讯质量，一般wifi顶多通讯100米。此外由于栅格地图直接开在内存内，如
果地图范围设置过大，容易占满内存导致其他程序运行缓慢。一般不建议超过50米*50米。

Q: 为什么要挡住D435的结构光？
A: 结构光的意义在于使相机得到的深度图更准确，但双目图片上会显示出位置固定不变的点阵光斑，这对VIO 的运行是不利的，所以需要关掉。

Q: VINS飘怎么办？
A: 1. 检查环境中是否有强反光物体（瓷砖、玻璃等）
2. 尽量缓慢地移动无人机，场景内不要有运动物体
3. 尽量准确地测量初始外参
4. 不要在运行vins的时候在远程桌面上运行rviz（会占用大量CPU资源），实在想开建议去配一下ROS 多机，然后在笔记本上开
5. 检查环境中是否有频闪光源（肉眼无法看出，在realsense的单目画面中检查）

Q: 我没有自稳模式无人机的飞行经验，身边也没有有经验的飞手，怎么办呢？
A: 1. 有预算的情况下，建议购买一台耐摔的带保护圈的穿越机来练手，推荐的型号有mobula6,吉朗小金鱼 85x,化骨龙racewhoop30等
2. 没啥预算的情况下，建议购买一个遥控器加密狗来把课程推荐的AT9S遥控器连接到电脑，然后在模拟 器里练熟。模拟器推荐steam上的liftoff,免费的推荐free rider

Q: 我想用NX做机载电脑，该另外做些什么？
A: 原则上不建议小白用NX，会多很多麻烦事，本课程并不涉及，助教也没有时间去帮你看。 需要额外做下面的事：
1. 修改VINS为GPU版本的，因为NX的CPU算力很差，跑课程的CPU版VINS一定跑不动
2. 解决NX固定及供电问题
3. 解决realsense固定问题
4. 解决NX用小底板时接口不够的问题
5. 解决一系列arm和x86不兼容带来的问题

Q: 我按照教程修改sd卡里的etc/extra.txt后，IMU频率没有变成200hz怎么办？ A: 可能原因是你的固件不支持这样修改，可以尝试在启动mavros后执行： rosrun mavros mavcmd long 511 105 5000 0 0 0 0 0 & sleep 1; rosrun mavros mavcmd long 511 31 5000 0 0 0 0 0 & sleep 1;

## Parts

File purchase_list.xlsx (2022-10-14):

设备
备注 |  | 类目 | 型号 | 数量 | 单价 | 总价 | 淘宝链接
 |  | 机架 | QAV250 + 简易脚架 | 1 | 48 | 48 | https://item.taobao.com/item.htm?spm=a1z0d.6639537.1997196601.4.7b117484yJpUkV&id=520738516076
预算充足建议这个 |  | 电调 | 银燕45A | 5 | 186 | 930 | https://item.taobao.com/item.htm?id=652264033077&ns=1&abbucket=3
 |  |  | 银燕30A | 5 | 75 | 375 | https://item.taobao.com/item.htm?id=544650621044&ns=1&abbucket=13
 |  | 电机 | Tmotor 2306 2400KV | 5 | 69 | 345 | https://item.taobao.com/item.htm?spm=a1z0d.6639537.1997196601.70.7b117484yJpUkV&id=640533613167
预算充足建议这个 |  |  | Tmotor F60 2550KV | 5 | 149 | 745 | https://item.taobao.com/item.htm?id=650719152882&ns=1&abbucket=13
课程内容仅介绍holybro pix4 mini的安装，其余飞控的安装大同小异，但最推荐的还是mini |  | 飞控 | Holybro pixhawk4 mini | 1 | 1269 | 1269 | https://item.taobao.com/item.htm?spm=a1z09.2.0.0.797e2e8dUtfEC6&id=585002966933&_u=332egecqdc8b
 |  |  | Holybro pixhawk4 | 1 | 1330 | 1330 | https://item.taobao.com/item.htm?id=622652205393&ns=1&abbucket=13
 |  |  | CUAV V5 NANO | 1 | ？ | ？ | 原价应该卖699，但淘宝上都是1099的，就不贴链接了
比较厚且长，安装可能遇到问题 |  |  | CUAV V5 | 1 | 1799 | 1799 | https://item.taobao.com/item.htm?spm=a1z10.5-c-s.w4002-22188405087.10.6be2688auoxM9A&id=594262853015
比较厚且长，安装可能遇到问题 |  |  | CUAV X7 | 1 | 1999 | 1999 | https://item.taobao.com/item.htm?spm=a1z10.5-c-s.w4002-22188405087.16.6be2688auoxM9A&id=617384615131
 |  | DC供电线 | XT60 | 2 | 13 | 26 | https://item.taobao.com/item.htm?spm=a1z09.2.0.0.773d2e8despLGo&id=613472402389&_u=g2epqo5e38f7
根据飞控接口型号购买，例如pix4 mini是micro usb，CUAV的是typec |  | 飞控连接线 | 双左弯0.15m | 2 | 9.5 | 19 | https://detail.tmall.com/item.htm?id=43144333772&_u=i32egecqf5d3&skuId=4498792030458
 |  | TYPEC连接线 | 15cm | 2 | 22.9 | 45.8 | https://detail.tmall.com/item.htm?id=617461584216&spm=a1z09.2.0.0.2abd2e8da0sHzh&_u=l32egecq0e19
 |  | 机载电脑 | Intel NUC 猛虎峡谷 准系统 i5 薄款 | 1 | 2590 | 2590 | https://item.taobao.com/item.htm?id=638758423001&ns=1&abbucket=3
内存条和固态类似型号都能用 |  |  | 三星 DDR4内存条 8G 3200hz | 1 | 229 | 229 | https://detail.tmall.com/item.htm?id=541378489978&spm=a1z09.2.0.0.ea4d2e8dwctqDn&_u=t2epqo5eaa9f
 |  |  | 影驰黑将 250G M.2固态硬盘 | 1 | 234 | 234 | https://detail.tmall.com/item.htm?id=541378489978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
7通道以上的遥控器和对应的SBUS接收机都能用，但设置方法不额外介绍 |  | 接收机 | 乐迪 R12DSM | 1 | 94 | 94 | https://item.taobao.com/item.htm?spm=a1z09.2.0.0.2abd2e8da0sHzh&id=541658831753&_u=l32egecq5116
 |  | 遥控器 | 乐迪 AT9S PRO 左手不回中 | 1 | 580 | 580 | https://item.taobao.com/item.htm?spm=a1z09.2.0.0.2abd2e8da0sHzh&id=533085053894&_u=l32egecq481a
碳板是定制的，把附件里的stp文件发给卖家即可 |  | 碳纤维板 | 上板+下板 | 1 | 150 | 150 | https://item.taobao.com/item.htm?spm=a1z09.2.0.0.797e2e8dUtfEC6&id=646866813960&_u=332egecqb666
 |  | HDMI欺骗器 |  | 1 | 3 | 3 | https://item.taobao.com/item.htm?id=600829968368&ali_trackid=1_b8192277632fc8796a134ac616741b67
必须买这个型号，可以刚好塞进机架里 |  | 电池 | 格氏 2300mAh 4S | 2 | 125 | 250 | https://item.taobao.com/item.htm?spm=a1z09.2.0.0.2abd2e8da0sHzh&id=583311920871&_u=l32egecq9cf8
 |  | TYPEC连接线 | 30cm | 2 | 27 | 54 | https://detail.tmall.com/item.htm?id=617461584216&spm=a1z09.2.0.0.2abd2e8da0sHzh&_u=l32egecq0e19
类似5寸桨都行 |  | 桨叶 | 乾丰51477 | 2 | 14 | 28 | https://item.taobao.com/item.htm?spm=a1z09.2.0.0.2abd2e8da0sHzh&id=627007813072&_u=l32egecqfabf
 |  | 5V稳压模块 | 5V工业级 | 2 | 11.5 | 23 | https://item.taobao.com/item.htm?spm=a1z09.2.0.0.797e2e8dUtfEC6&id=590892957814&_u=332egecq63c6
 |  | 双目深度相机 | INTEL REALSENSE D435 | 1 | 2180 | 2180 | https://item.taobao.com/item.htm?spm=a1z10.1-c.w4004-8474743471.36.1f164e1fL0mvDM&id=670494420704
根据个人情况选购 |  | 5寸桨保 |  | 2 | 10 | 20 | https://item.taobao.com/item.htm?id=574989413314&ns=1&abbucket=13
 |  | 短路保护器 |  | 1 | 30 | 30 | https://item.taobao.com/item.htm?id=656973651729&ns=1&abbucket=19
 | 耗材 | 硅胶线 | 20,18,14AWG | 若干 |  |  | https://item.taobao.com/item.htm?id=631990884181&ns=1&abbucket=3
 |  | BB响 |  | 1 |  |  | https://item.taobao.com/item.htm?id=13954041762&ns=1&abbucket=3
 |  | 硅胶杜邦线 | 10cm,15cm，公对母 | 若干 |  |  | https://item.taobao.com/item.htm?id=567943637652&ali_trackid=1_82cb0cae98e77d6ab8f389660ffac1cf
 |  | XT60母头 |  | 1
 |  | 双通铝柱 | M3*8/10/15/20的各买4根以上 |  |  |  | https://item.taobao.com/item.htm?id=603331087035&ns=1&abbucket=13
 |  | 3M双面胶 | 20mm*3m | 1 |  |  | https://detail.tmall.com/item.htm?id=653733592411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
 |  | 螺丝 | M3*6mm 扁头 |  |  |  | https://detail.tmall.com/item.htm?id=624811454452&_u=i32egecq19dc&skuId=4601948603338
工具
 |  | 类目 | 型号 | 单价 | 数量 | 总价 | 链接
 |  | 烙铁 | AT937标配 | 143 | 1 | 143 | https://item.taobao.com/item.htm?id=7800035658&ns=1&abbucket=14
 |  | 烙铁头 | 900M-1.6K | 11 | 1 | 11 | https://item.taobao.com/item.htm?spm=a1z10.3-c-s.w4002-23344838098.27.754f1004qeCAY6&id=579728085148
 |  | 海绵 |  | 2 | 1 | 2 | https://item.taobao.com/item.htm?spm=a1z10.3-c-s.w4002-23344838098.9.6d6c1004U43LPK&id=7586598250
 |  | 焊锡 | 0.5mm 500g | 76.67 | 1 | 76.67 | https://detail.tmall.com/item.htm?spm=a230r.1.14.11.552520bejLfPiP&id=43741015860&ns=1&abbucket=14
 |  | 夹持台 | 褐色 | 75 | 1 | 75 | https://item.taobao.com/item.htm?id=613902998667&ali_trackid=1_a8d9bfa88456e4bdeb5141959028dacf
 |  | 扳手 |  | 11 | 1 | 11 | https://item.taobao.com/item.htm?id=610029436080&ns=1&abbucket=14
 |  | 螺丝刀 | 2.0mm、2.5mm | 10.99 | 1 | 10.99 | https://detail.tmall.com/item.htm?id=572329178882&cm_id=140105335569ed55e27b&abbucket=14
 |  | 万用表 |  | 49 | 1 | 49 | https://item.jd.com/100000287597.html
 |  | 剪刀 | 3把中号 | 10.9 | 0.33 | 3.597 | https://item.jd.com/6020791.html
 |  | 切割垫 | A3 | 19.9 | 1 | 19.9 | https://item.jd.com/100001317628.html
 |  |  |  |  |  | 15345.8

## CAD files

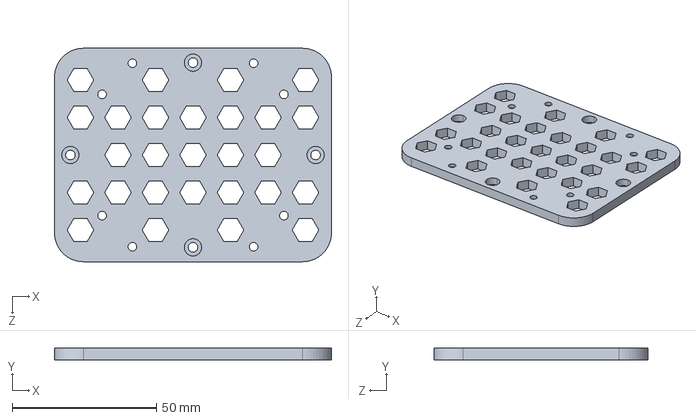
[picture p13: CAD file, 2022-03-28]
carbon_board/底板.STEP
96.0 x 4.00 x 74.0 mm

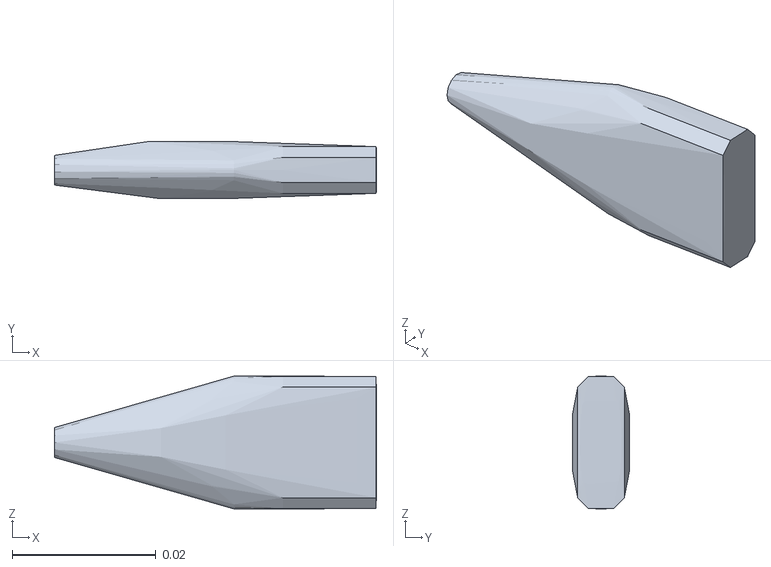
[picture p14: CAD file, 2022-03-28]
src/realflight_modules/realsense-ros/realsense2_description/meshes/plug_collision.stl
0.0448 x 0.008 x 0.0185

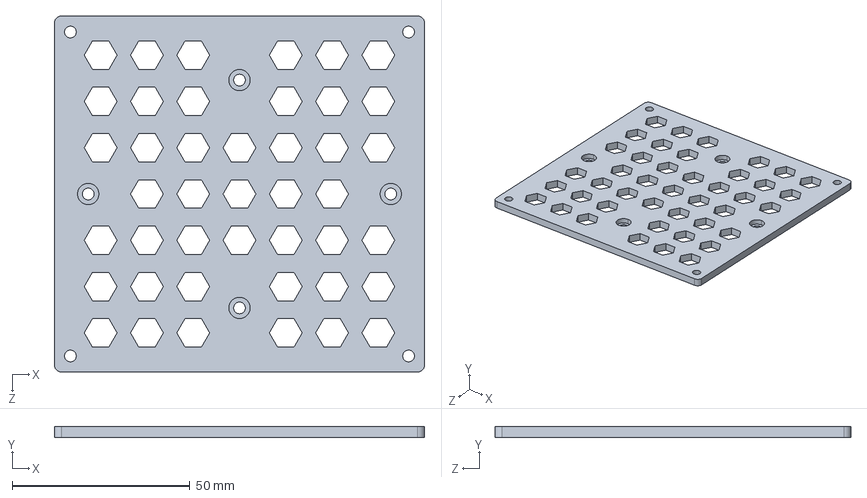
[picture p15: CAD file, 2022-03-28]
carbon_board/顶板.STEP
104.0 x 3.00 x 100.0 mm

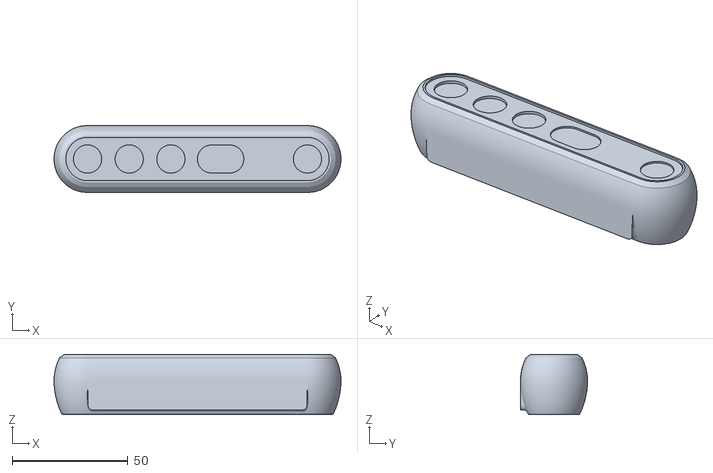
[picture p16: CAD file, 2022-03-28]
src/realflight_modules/realsense-ros/realsense2_description/meshes/d455.stl
124.0 x 29.0 x 26.0

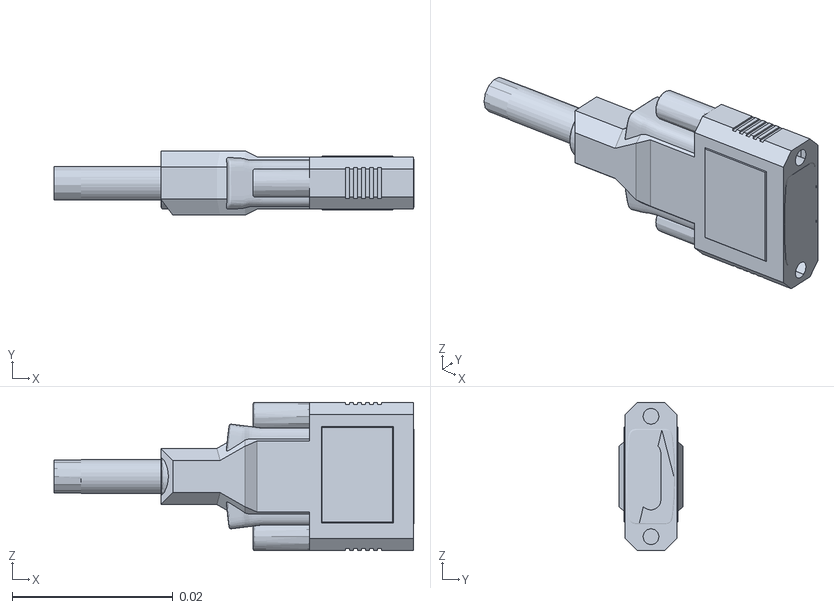
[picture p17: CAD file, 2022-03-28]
src/realflight_modules/realsense-ros/realsense2_description/meshes/plug.stl
0.0448 x 0.008 x 0.0185

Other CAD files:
carbon_board/底板.STL
carbon_board/顶板.STL

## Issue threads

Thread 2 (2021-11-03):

Few Questions regarding the setup

FaboNo, 2021-11-03:
First thank you very much for providing all these information! It is very helpful for students and researchers.
I have few question

1. Can you tell us please what are the characteristics of the tri-blades you are using? I cannot find it in the shopping list - or I missed it ...
2. From what I can see the total weight of the drone fully assembled should be around 1.7/1.8 kg probably. I am wondering what is the thrust delivered by the T-motor KV 2550 at 50%/ 60% throttle ? I tried to find out on Internet but cannot... and the related question is about the autonomy - is it around 5 mn or more?
3. You are not mentioning what kind of geometric controller are you using?  Can you tell us more about it?
4. As you are using PX4 and dynamic trajectories, it is pretty important to have the "PX4  rate controller"  pretty well tuned.  is it possible for you to share your params file ?

Thanks again for all the fantastic open you are sharing with the community

PanNeng-ZJU, 2021-11-09:
@FaboNo Hello, thanks for your advise.
1.Various types from GEMFAN work. For example, the 5147, 5144 tri-blades are fine.
2.The weight of the fully assembled drone is around 1.1kg in fact. You can look up the thrust-efficiency table at https://uav-cn.tmotor.com
3.We use the SO(3) px4 controller onboard. And for this part, I'm afraid we can't open-source it.
4.The params file and the corresponding firmware are already updated.

roam-water, 2021-11-15:
首先非常感谢你们提供的信息，请问一下，我组装的qav250机子跟您的重量也是11.1kg，但是我推油门时候总是上升或者下降很快（动力太大啦），非常难控制，请问您是怎么调试让无人机平稳上升，然后油门控制比较柔和，动作顺畅的呢，是修改PWM_MAIN_RATE 吗，还是做出了什么样的修改，期待你的回答，同时非常感谢您抽出时间阅读我的留言，祝您快乐！

PanNeng-ZJU, 2021-11-22:
@roam-water  如果你是用pwm控制电机的话，可以通过修改pwm_main_rate来解决这个问题，但这个教程里是用dshot控制电机的。可以通过地面站里调节飞机的悬停油门来解决这个问题。

ZhangBihui0311, 2022-02-25:
@PanNeng-ZJU
请问能否解释一下“SO(3) px4 controller”，它和PX4发行的不同版本firmware有什么关系？
另外还想请问作者是否采用了PX4的offboard控制模式？我在自己的实验中感觉不同固件版本对offboard支持很不稳定。
谢谢！

roam-water, 2022-03-21:
谢谢，非常感谢

在 2022年2月25日星期五，ZhangBihui0311 ***@***.***> 写道：

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

Closed 2021-11-22.

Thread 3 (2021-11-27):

有关可选购的飞控和机载电脑

J1dan, 2021-11-27:
你们好，请问可选购的三种飞控有什么使用上的区别吗？是否有更推荐的一种？
另一个问题是关于Xavier NX，官方套件就是核心板+底板，那么还需要再购买表中的NX载板吗？是否有什么不同？
谢谢！

PanNeng-ZJU, 2021-11-29:
@J1dan
1.个人更推荐CUAV NORA，因为体积相较其他两款更小一些，性能上都比较相似。
2.表中的载板体积更小，更适合使用在无人机上，但相应的USB接口也更少，如果您对机载电脑体积没有要求，可以不购买额外的载板。另外官方的底板不太好固定在飞机上，可能需要用比较厚的海绵胶粘起来

J1dan, 2021-11-29:
非常感谢您！

J1dan, 2021-11-30:
您好，再请问一下如果是购买NX载板的话，是不是就只需要购买NX核心板然后装上去就可以了？也就是说不需要购买NX开发板？我看价目表里的Xavier NX价格是6800，但核心板的价格只要3699，所以有点好奇如果另买载板的话是否还是需要购买开发者套件。

PanNeng-ZJU, 2021-11-30:
我的建议是不缺预算的话购买开发者套件。因为单独购买的核心板是不能插SD卡的，装系统的SD卡必须插在NX载板上，而这需要另打驱动，比较麻烦。开发者套件里的核心板是支持SD卡的，可以即插即用

------------------&nbsp;原始邮件&nbsp;------------------
发件人:                                                                                                                        "ZJU-FAST-Lab/Fast-Drone-250"                                                                                    ***@***.***&gt;;
发送时间:&nbsp;2021年11月30日(星期二) 上午10:02
***@***.***&gt;;
抄送:&nbsp;"自动化（交叉）1701 ***@***.***&gt;;"State ***@***.***&gt;;
主题:&nbsp;Re: [ZJU-FAST-Lab/Fast-Drone-250] 有关可选购的飞控和机载电脑 (Issue #3)

您好，再请问一下如果是购买NX载板的话，是不是就只需要购买NX核心板然后装上去就可以了？也就是说不需要购买NX开发板？我看价目表里的Xavier NX价格是6800，但核心板的价格只要3699，所以有点好奇如果另买载板的话是否还是需要购买开发者套件。

—
You are receiving this because you modified the open/close state.
Reply to this email directly, view it on GitHub, or unsubscribe.
Triage notifications on the go with GitHub Mobile for iOS or Android.

J1dan, 2021-11-30:
谢谢解答，但是我还是有点迷惑：之前您说表中的载板体积更小，我理解为更推荐使用表中的载板；但是如果购买开发板的话，不是就不需要另外的载板了吗？
或者换句话说，我现在不缺预算，那么是不是更推荐购买开发者套件加上表中889的载板？还是只需要开发者套件，或官方核心板+889载板？麻烦您建议一下。麻烦您了！

PanNeng-ZJU, 2021-11-30:
购买开发者套件+889的载板，把开发者套件里的核心板拆出来装在889的载板上

------------------&nbsp;原始邮件&nbsp;------------------
发件人:                                                                                                                        "ZJU-FAST-Lab/Fast-Drone-250"                                                                                    ***@***.***&gt;;
发送时间:&nbsp;2021年11月30日(星期二) 中午12:22
***@***.***&gt;;
抄送:&nbsp;"自动化（交叉）1701 ***@***.***&gt;;"State ***@***.***&gt;;
主题:&nbsp;Re: [ZJU-FAST-Lab/Fast-Drone-250] 有关可选购的飞控和机载电脑 (Issue #3)

谢谢解答，但是我还是有点迷惑：之前您说表中的载板体积更小，我理解为更推荐使用表中的载板；但是如果购买开发板的话，不是就不需要另外的载板了吗？
 或者换句话说，我现在不缺预算，那么是不是更推荐购买开发者套件加上表中889的载板？还是只需要开发者套件，或官方核心板+889载板？麻烦您建议一下。麻烦您了！

—
You are receiving this because you modified the open/close state.
Reply to this email directly, view it on GitHub, or unsubscribe.
Triage notifications on the go with GitHub Mobile for iOS or Android.

J1dan, 2021-11-30:
谢谢，刚才去问了一下开发板的卖家，但他们说开发板的SD卡也是插在底板上的，所以单卖的核心板和开发板上的核心板应该没有区别；而889载板的卖家说可以在他们家买核心板+他们的底板，可以帮忙装好ubuntu系统，随后我们再自己装SD卡，根据他们的教程设置从SD卡启动系统。请问您觉得这个方案怎么样？

PanNeng-ZJU, 2021-11-30:
可以的

------------------&nbsp;原始邮件&nbsp;------------------
发件人:                                                                                                                        "ZJU-FAST-Lab/Fast-Drone-250"                                                                                    ***@***.***&gt;;
发送时间:&nbsp;2021年11月30日(星期二) 下午2:37
***@***.***&gt;;
抄送:&nbsp;"自动化（交叉）1701 ***@***.***&gt;;"State ***@***.***&gt;;
主题:&nbsp;Re: [ZJU-FAST-Lab/Fast-Drone-250] 有关可选购的飞控和机载电脑 (Issue #3)

谢谢，刚才去问了一下开发板的卖家，但他们说开发板的SD卡也是插在底板上的，所以单卖的核心板和开发板上的核心板应该没有区别；而889载板的卖家说可以在他们家买核心板+他们的底板，可以帮忙装好ubuntu系统，随后我们再自己装SD卡，根据他们的教程设置从SD卡启动系统。请问您觉得这个方案怎么样？

—
You are receiving this because you modified the open/close state.
Reply to this email directly, view it on GitHub, or unsubscribe.
Triage notifications on the go with GitHub Mobile for iOS or Android.

Closed 2021-11-29.

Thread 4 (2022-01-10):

大佬您好，想请教一下关于机载处理器功率的问题 Some questions about onboard processer power

dssdyx, 2022-01-10:
您好，想请教一下，平台使用Manifold 2C运行vins Fusion和ego planner或ego swarm时，有几个问题
1. 平台供电问题，我看manifold是15.2-27v宽压输入的，但是平台使用的是4s电池，处理器是怎么供电的呢，是通过电池直接供电还是通过稳压器，如果功率太大导致电压降到15.2v以下会不会导致处理器断电，问这个问题主要是想知道大佬你们是怎么平衡性能、功率和供电的。
2.  功率问题，处理器电源管理是否需要开到performance状态呢，我看高飞老师在ego planner里建议采用performance状态去保证系统不降频，但这样运行会导致处理器功率很高，如果电池容量只有2300mah，运行demo时，大佬你们一般能飞多久啊。
3. 现在manifold 2c停产了，nx的性能也不是那么理想，大佬你们有意向替换处理器么？

PanNeng-ZJU, 2022-01-14:
1.你说的问题确实存在,妙算2c由于一些产品本身的设计原因,在低电压(例如飞机炸鸡时,电机电流过大导致电源压降很大)时会关机,这个问题即使使用6S电池也会出现,如果想彻底解决这个问题,可以使用一个升压模块把电源电压升到20V以上来给妙算供电,实测极端情况也不会导致妙算关机.
2.机载电脑的功率相较于电机的功率是很小的,开不开高功率模式都对续航影响不大.运行demo时,续航一般在5分钟以上,是这种构型无人机的正常水平.
3.可以考虑使用比较轻薄的nuc,我们实验室也正在对nuc进行测试

Closed 2022-01-14.

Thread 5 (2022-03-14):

您好，想向您请教一下关于飞控和机载计算机的通信线路问题

yangy-98, 2022-03-14:
您好，想请教一下，请问您们在对飞控和机载计算机通信时，用的是什么设备线路呢？我看PX4官网推荐了mRo USB FTDI Serial to JST-GH (Basic)，但似乎买不到这样的线路。
希望能收到您的回复，感谢！

PanNeng-ZJU, 2022-03-14:
用普通的能传输数据的usb线就可以，例如cuav的飞控一般是typec口的，就用typec-usbA的线就行

yangy-98, 2022-03-14:
感谢您的回复！

还想再请教您一下，目前我在用的飞控和机载计算机是pixhawk+nuc，我找了一下它们之间的通信方式，网络上似乎都是将机载计算机用usb转串口连接pixhawk上的telem2端口来进行的通信，

我之前也关注到您有用nuc主机的打算，不知您是否了解pixhawk+nuc的通信方式，以上所述是唯一方式？还是您所说的用普通的能传输数据的usb线就可以？

再次期待能够收到您的回复，感谢！

yangy-98, 2022-03-20:
> 用普通的能传输数据的usb线就可以，例如cuav的飞控一般是typec口的，就用typec-usbA的线就行

感谢您的回复！

还想再请教您一下，

1. 目前我在用的飞控和机载计算机是pixhawk+nuc，我找了一下它们之间的通信方式，网络上似乎都是将机载计算机用usb转串口连接pixhawk上的telem2端口来进行的通信，我之前也关注到您有用nuc主机的打算，不知您是否了解pixhawk+nuc的通信方式，以上所述是唯一方式？还是您所说的用普通的能传输数据的usb线就可以？

2. 请问您们是如何解决飞控和机载计算机的供电问题的？是用一块航模电池通过分电板的方式给它们供电的吗？

期待能够再次收到您的回复，感谢！

YU-TON, 2022-04-07:
1.用telem2需要usb转ttl的线连起来，我之前就是这么连的，也可以飞控的micro usb连到计算机的usb
2.教程里供电就是直接插电源
我这有一个疑问，直接插电源的话会不会在飞机降落的时候有大电流对计算机造成损坏，因为我之前有一架飞机的jetson NX是连到一个有过电流保护的12v稳压模块，每次降落螺旋桨停转瞬间计算机就会自动关机，我想是因为电压或者电流波动幅度过打导致稳压模块自动断电，那么如果不接稳压，这个波动是不是会对计算机有较大的损坏呢
@yangy-98 @PanNeng-ZJU

yangy-98, 2022-04-07:
非常感谢您们二位的回复，
关于稳压模块我暂时还没有用上，我目前使用的似乎是旧版的nuc，光供电电压好像就需12v了，目前还在初步测试中。
@PanNeng-ZJU @YU-TON

Closed 2022-03-14.

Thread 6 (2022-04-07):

heading issue

skyaid, 2022-04-07:
Hello, thank you for a great project.

When switching the current Px4ctrl to offboard, it rotates 180 degrees.

We start by looking at the back of the aircraft, but if we change to offboard

The aircraft sees us.

When looking at vio and ego planer rviz, the initial position is correct.

PanNeng-ZJU, 2022-04-07:
What is the odometry you use? Did you check the odometry's coordinate system si correct?

skyaid, 2022-04-07:
I used vins fusion gpu and odometry coodinate position is correct

I replaced the estimator file and visualization file using vins fusion provided by zju

PanNeng-ZJU, 2022-04-07:
Sorry, I have no idea where the problem lies @skyaid

skyaid, 2022-04-08:
@PanNeng-ZJU thanks

Closed 2022-04-08.

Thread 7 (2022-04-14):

运行ego-planner出现的问题

SSZ1, 2022-04-14:
您好！我一直都在关注你们组。首先非常感谢您能够开源自主无人机，可以预见到一定能够带动国内专业领域的发展。我在NUC上配置ego-planner这一步时，按照你们给的命令，编译完成，并且执行了`source devel/setup.bash`
在执行`roslaunch ego_planner sing_run_in_sim.launch`时报错：

**RLException: [sing_run_in_sim.launch] is neither a launch file in package [ego_planner] nor is [ego_planner] a launch file name
The traceback for the exception was written to the log file.**

请问为什么会出现这个问题，该怎么解决呢？十分感谢
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

xzqiaochu, 2022-04-16:
您好，似乎是拼写错误：single误拼成了sing
正确的写法：roslaunch ego_planner single_run_in_sim.launch
如果解决了记得close一下哈

SSZ1, 2022-04-17:
>

谢谢您！已经解决了，之前好像是看了没更新的readme.md，现在已经更新了，非常感谢！！！

Closed 2022-04-17.

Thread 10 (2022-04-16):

又发现几处笔误

xzqiaochu, 2022-04-16:
第十章 - VINS外参精确自标定
rostopic echo /**vins_estimator**/imu_propagate -> rostopic echo /**vins_fusion**/imu_propagate
(还有一处在 第十一章 - 自动起飞)

第十一章 - Ego-Planner实验
roslaunch **ego-planner** single_run_in_exp.launch -> roslaunch **ego_planner** single_run_in_exp.launch

PanNeng-ZJU, 2022-04-18:
感谢，已修改

Closed 2022-04-18.

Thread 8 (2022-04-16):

发现两处笔误

xzqiaochu, 2022-04-16:
第八章
VScode：sudo dpkg **--i** ***.deb  ->  VScode：sudo dpkg **-i** ***.deb
rosrun plotjuggler **plotjugller**  -> rosrun plotjuggler **plotjuggler**

anyway，感谢这门课程，学到了好多东西

PanNeng-ZJU, 2022-04-18:
感谢，已修改

Closed 2022-04-18.

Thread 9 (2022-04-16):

CMake Error at /lib/x86_64-linux-gnu/cmake/realsense2/realsense2Config.cmake:11 (message):   File or directory //include referenced by variable realsense2_INCLUDE_DIR   does not exist !

Shirleytyf, 2022-04-16:
用虚拟机安装了两次都报了相同的错，点进了/lib/x86_64-linux-gnu/cmake/realsense2/realsense2Config.cmake文件将错误的行注释之后还是会出现新的错误，明明一步步按着要求做的，真不知道是哪出问题了（之前在双系统装啥问题没有），但双系统没那么方便，求求了，救救孩子吧。

```
-- +++ processing catkin package: 'odom_visualization'
-- ==> add_subdirectory(uav_simulator/odom_visualization)
-- Using these message generators: gencpp;geneus;genlisp;gennodejs;genpy
-- +++ processing catkin package: 'local_sensing_node'
-- ==> add_subdirectory(uav_simulator/local_sensing)
-- Using these message generators: gencpp;geneus;genlisp;gennodejs;genpy
CMake Warning at /opt/ros/noetic/share/catkin/cmake/catkin_package.cmake:166 (message):
  catkin_package() DEPENDS on 'Eigen' but neither 'Eigen_INCLUDE_DIRS' nor
  'Eigen_LIBRARIES' is defined.
Call Stack (most recent call first):
  /opt/ros/noetic/share/catkin/cmake/catkin_package.cmake:102 (_catkin_package)
  uav_simulator/local_sensing/CMakeLists.txt:72 (catkin_package)

-- +++ processing catkin package: 'mockamap'
-- ==> add_subdirectory(uav_simulator/mockamap)
-- Using these message generators: gencpp;geneus;genlisp;gennodejs;genpy
-- +++ processing catkin package: 'realsense2_camera'
-- ==> add_subdirectory(realflight_modules/realsense-ros/realsense2_camera)
-- Using these message generators: gencpp;geneus;genlisp;gennodejs;genpy
CMake Error at /lib/x86_64-linux-gnu/cmake/realsense2/realsense2Config.cmake:11 (message):
  File or directory //include referenced by variable realsense2_INCLUDE_DIR
  does not exist !
Call Stack (most recent call first):
  /lib/x86_64-linux-gnu/cmake/realsense2/realsense2Config.cmake:33 (set_and_check)
  realflight_modules/realsense-ros/realsense2_camera/CMakeLists.txt:44 (find_package)

-- Configuring incomplete, errors occurred!
See also "/home/tan/文档/Fast-Drone-250-master/build/CMakeFiles/CMakeOutput.log".
See also "/home/tan/文档/Fast-Drone-250-master/build/CMakeFiles/CMakeError.log".

```

Closed 2023-04-12.

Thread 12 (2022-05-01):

在px4ctrl的controller.cpp中有一处代码没理解

z1047941150, 2022-05-01:
[https://github.com/ZJU-FAST-Lab/Fast-Drone-250/blob/master/src/realflight_modules/px4ctrl/src/controller.cpp](https://github.com/ZJU-FAST-Lab/Fast-Drone-250/blob/master/src/realflight_modules/px4ctrl/src/controller.cpp)
从48行开始
Eigen::Quaterniond q = Eigen::AngleAxisd(des.yaw,Eigen::Vector3d::UnitZ())
        * Eigen::AngleAxisd(pitch,Eigen::Vector3d::UnitY())
        * Eigen::AngleAxisd(roll,Eigen::Vector3d::UnitX());
 u.q = imu.q * odom.q.inverse() * q;
不明白为什么需要这样才能得到u.q
求大佬们指导

z1047941150, 2022-05-01:
两两相乘我能理解，比如imu.q * odom.q.inverse()，就是把imu的姿态表示在odom姿态坐标下，但是三个相乘，我就有点懵了

z1047941150, 2022-05-05:
因为飞控的姿态是以imu为准的，而odom和imu肯定是有个差值的，期望的位姿（des）是在odom基础上得来的。所以再下发给飞控的时候，我们需要先把期望姿态变到imu坐标下。
解决喽~~~

Closed 2022-05-05.

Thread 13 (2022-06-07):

CUAV X7+飞控

meyiao, 2022-06-07:
您好，买了purchase_list里边链接的x7飞控，买到才发现其实是x7+。烧不进去给的固件，请问用px4 v1.12.3以后的固件可以吗？有哪里要修改的吗？
谢谢!

albert17github, 2022-07-10:
您好，我使用的也是CUAV x7+飞控，希望对您有点帮助。
首先，这个项目文件下的飞控固件是给V5使用的，x7+不能使用。
如果要用x7+飞控，得自己再下载PX4的固件：
PX4固件下载链接： https://github.com/PX4/PX4-Autopilot/releases
试了一下，使用v1.13的固件时，imu的频率有点问题。
我用的是**x7pro v1.11**的固件，目前来看，没有遇到什么问题。

albert17github, 2022-07-10:
> 您好，买了purchase_list里边链接的x7飞控，买到才发现其实是x7+。烧不进去给的固件，请问用px4 v1.12.3以后的固件可以吗？有哪里要修改的吗？ 谢谢!

您好，我使用的也是CUAV x7+飞控，希望对您有点帮助。
首先，这个项目文件下的飞控固件是给V5使用的，x7+不能使用。
如果要用x7+飞控，得自己再下载PX4的固件：
PX4固件下载链接： https://github.com/PX4/PX4-Autopilot/releases
试了一下，使用v1.13的固件时，imu的频率有点问题。
我用的是x7pro v1.11的固件，目前来看，没有遇到什么问题。

meyiao, 2022-07-11:
> > 您好，买了purchase_list里边链接的x7飞控，买到才发现其实是x7+。烧不进去给的固件，请问用px4 v1.12.3以后的固件可以吗？有哪里要修改的吗？ 谢谢!
>
> 您好，我使用的也是CUAV x7+飞控，希望对您有点帮助。 首先，这个项目文件下的飞控固件是给V5使用的，x7+不能使用。 如果要用x7+飞控，得自己再下载PX4的固件： PX4固件下载链接： https://github.com/PX4/PX4-Autopilot/releases 试了一下，使用v1.13的固件时，imu的频率有点问题。 我用的是x7pro v1.11的固件，目前来看，没有遇到什么问题。

感谢大佬，我有时间试试！

Closed 2022-07-11.

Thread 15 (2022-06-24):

关于算法中使用的imu问题

SSZ1, 2022-06-24:
已经把整个项目跑起来了，但是遇到了一些问题，想咨询一下。

1.自主飞行项目中的vins使用的imu是飞控的imu，想咨询一下为什么不直接使用realsense的imu？

2.我在实机实验中，运行vins，发现vins特别容易漂，飞机自动起飞时候飞行不稳可能也与之有关。想问一下vins为什么会这么容易漂？

3.因为2中的问题，我尝试把项目中vins中接入的imu换成了realsense自带的imu，单独运行vins算法，发现没有那么容易漂了，但是在rviz中发现，它的坐标轴变动了，y轴变成垂直方向了，开了realsense-viewer才发现，realsense默认是y轴在垂直方向的，请问这是不是你们选择使用飞控imu的原因。

PanNeng-ZJU, 2022-07-29:
1.realsense的imu没有做减震，噪声较大
2.外参标定得不对
3.如果外参标定得不对，realsense的imu由于与相机本身位移较少，所以不容易飘。 是

Closed 2022-07-29.

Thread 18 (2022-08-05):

运行roslaunch vins fast_drone_250.launch时报错

albert17github, 2022-08-05:
运行roslaunch vins fast_drone_250.launch时报错
报错内容：
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
环境：JetsonXavierNX Ubuntu18
步骤：VINS外参精确自标定：sh shfiles/rspx4.sh
前面测试验证都通过了，这个报错有点不明白，麻烦指教，谢谢！

albert17github, 2022-08-05:
我换成VINS-GPU就没有这个问题了
已关闭

Closed 2022-08-05.

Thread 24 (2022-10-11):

请问编译好的px4_fmu-v5_default.px4是没有定点模式吗？另外关于不同固件imu频率发布问题

goodworth1, 2022-10-11:
我用你们提供的固件，在添加GPS模块后，无法进入定点模式。另外我尝试了1.13版本，imu根据你们提供的命令去修改发布频率，结果发现只有50HZ左右，明显发布频率修改没有生效，在你们提供的1.11版本是可以的。如果要使用1.13固件，要怎么修改发布频率呢？你们现在有尝试使用最新pixhawk6C进行试验吗？

PanNeng-ZJU, 2022-10-14:
1. 启动mavros后尝试一下以下命令：
rosrun mavros mavcmd long 511 105 5000 0 0 0 0 0 & sleep 1;
rosrun mavros mavcmd long 511 31 5000 0 0 0 0 0 & sleep 1;

2.没有

Closed 2022-10-14.

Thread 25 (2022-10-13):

找不到参数dshot_config

LiangtaoZhong, 2022-10-13:
作者，您好，我使用v1.11.0的px4_fmu_v2的固件，找不到dshot_config参数，不能使用dshot协议电调。换成v1.13.0就能找到该参数。而您又提到v1.13有BUG，请问是致命性BUG吗？是否可以使用v1.13固件呢？谢谢

PanNeng-ZJU, 2022-10-14:
我仅在v5的1.11固件上测试通过，其他版本的固件可能可以，你可以试试

LiangtaoZhong, 2022-10-14:
好的 谢谢

Closed 2022-10-14.

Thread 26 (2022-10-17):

自动起飞失败

Chai8226, 2022-10-17:
自动起飞报错：[px4ctrl] Reject AUTO_TAKEOFF. If you have your RC connected, keep its switches at "auto hover" and "command control" states, and all sticks at the center, then takeoff again.
请教一下怎么办，通道没选择错误

DB-PLPSlame, 2022-12-28:
你好，请问这个报错解决了吗，我也遇到了同样的错误

zhao6868999, 2025-04-07:
Hello, I have also encountered this problem. How did you solve it？

Closed 2022-10-18.

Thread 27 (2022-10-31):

sh rspx4.sh 一段时间后出现wait for imu

cbyf, 2022-10-31:
> 1

.用rostopic hz /mavros/imu/data_raw 检查频率为190hz（刚刚开始时会从150hz逐渐上升）。拿起飞机来回走的过程中会出现**wait for imu**。
问题如图
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

> 2
在标定外参前需要大概估计双目相对与imu的位置，请问坐标系是东北天还是前右下，或是左手系右手系？
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

PanNeng-ZJU, 2022-11-09:
1. wait for imu是因为imu预积分和特征点匹配间相差太远，说明已经飘了

2. 右手系 x前 y左 z上

cbyf, 2022-11-12:
请问如何改善imu预积分和特征点匹配间相差太远的问题呢？谢谢

PanNeng-ZJU, 2022-11-14:
@cbyf 参考Q&A中的 “VINS飘怎么办？”

qingbyin, 2023-03-01:
Hi @PanNeng-ZJU,
看到这个回复有些疑惑，请教下无人机IMU的坐标系通常是[NED](https://docs.px4.io/main/en/config/flight_controller_orientation.html) ，为什么这里机体坐标系是前左上呢?并且这样约定的话，那IMU也要重新设定为z朝上了?

70loKirin, 2023-03-12:
你好，请问你解决了吗，最近我也在尝试，跟你一样出现过wait for imu的情况，我目前最大的疑点是旋转矩阵的填法，因为视频中飞控和相机有一个90度的差值，但是在我的飞机上二者都朝前
请问你知道这种情况下旋转矩阵怎么填吗
以及我也想知道原理，即imu和相机的坐标系是怎样的，我到现在还没有根据他给出的这个矩阵反推出二者的关系，网上的资料说法太多了（比如相机是否是右x下y前z 或是普通的前x左y右z   imu的方向也是 ned还是普通的情况？）
打扰抱歉 但这真的很困扰我

bulingda, 2023-04-04:
> 你好，请问你解决了吗，最近我也在尝试，跟你一样出现过wait for imu的情况，我目前最大的疑点是旋转矩阵的填法，因为视频中飞控和相机有一个90度的差值，但是在我的飞机上二者都朝前 请问你知道这种情况下旋转矩阵怎么填吗 以及我也想知道原理，即imu和相机的坐标系是怎样的，我到现在还没有根据他给出的这个矩阵反推出二者的关系，网上的资料说法太多了（比如相机是否是右x下y前z 或是普通的前x左y右z imu的方向也是 ned还是普通的情况？） 打扰抱歉 但这真的很困扰我

请问你解决了吗？

qllokirin, 2023-04-04:
> > 你好，请问你解决了吗，最近我也在尝试，跟你一样出现过wait for imu的情况，我目前最大的疑点是旋转矩阵的填法，因为视频中飞控和相机有一个90度的差值，但是在我的飞机上二者都朝前 请问你知道这种情况下旋转矩阵怎么填吗 以及我也想知道原理，即imu和相机的坐标系是怎样的，我到现在还没有根据他给出的这个矩阵反推出二者的关系，网上的资料说法太多了（比如相机是否是右x下y前z 或是普通的前x左y右z imu的方向也是 ned还是普通的情况？） 打扰抱歉 但这真的很困扰我
>
> 请问你解决了吗？

嗯，忘记跟进了，我认为主要问题就是齐次变换矩阵中的旋转矩阵
简而言之，使用px4的imu和d435i前视就直接按照视频里的填即
[0 0 1
-1 0 0
0 -1 0]（无论飞控朝向哪边安装，飞控会在校准的时候知晓前方的位置，最终发布的imu都是一样的
但括号内的内容我没有测试过 只是推测）
（相机坐标系右x下y前z  px4的imu是前x左y上z 自行计算一下 旋转矩阵就是上面那个）
然后如果没有光源频闪（rqt_image_view仔细看看）且特征点足够，就不会出现了，多次标定把矩阵填准就好了

Closed 2022-11-09.

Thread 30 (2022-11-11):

陀螺仪零偏警告；路径规划路线异常

cbyf, 2022-11-11:
1. gyroscope bias initial calibration -0.00056661 0.00100545 -0.000996476
是一个警告，请问有影响吗？
2.如下图，路径规划路线异常，无人机往所规划路径的方向飘（但机头不会朝着运动的方向，看起来似乎机头不会转动，因为正常情况下，机头总朝向运动方向），请问如何解决，谢谢。
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

PanNeng-ZJU, 2022-11-14:
1.没有见过这种警告，看起来问题不大
2.能提供视频吗？文字描述看不出来

Closed 2023-04-12.

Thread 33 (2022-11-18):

PX4 Cntrl changes

EhrazImam, 2022-11-18:
Hi, I hope you are doing well as i can see here @https://github.com/ZJU-FAST-Lab/Fast-Drone-250/blob/8ff64274b161bb829653faf5946656658e7e2c9f/src/realflight_modules/px4ctrl/src/px4ctrl_node.cpp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 why we cant use /mavros/imu/data_raw. As what i know difference between these two is one gives you orientation and one doesn't as we have already switched off the magnetometer why we are using it.
Thank you

PanNeng-ZJU, 2022-11-30:
The orientation of imu is used in the 51 line of [controller.cpp](https://github.com/ZJU-FAST-Lab/Fast-Drone-250/commit/394bfdfad137e4dc234f30e9270b99110c19c764):
u.q = imu.q * odom.q.inverse() * q;

Closed 2022-11-30.

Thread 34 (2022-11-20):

VINS时间同步

panpanyunshi, 2022-11-20:
感谢实验室的工作，使用过程有些问题想再请教您们。
就是多次使用PX4+D435，VINS偶尔会启动不稳定，或起飞后也有不小飘逸。
看了VINS介绍说可以做硬件时间同步来提高性能
想请教下，用pX4和D435可以做时间同步吗，会不会对性能有提升呢，有没有一些链接资料可以供参考的呢
真的感谢哈

PanNeng-ZJU, 2022-11-30:
@YangTiankai 请凯哥来解答一下

dssdyx, 2023-01-11:
@panpanyunshi 可能是你的PX4传感器没有校准好，或者内部参数有问题，你用多少版本的飞控

panpanyunshi, 2023-01-13:
感谢大佬的回答，用的是雷迅V5飞控，校准是参考px4的教程。想问下标定完后，应该看哪些参数来判断结果的好坏呢。再次感谢哈

dongdongbh, 2023-01-13:
可以同步，参考[Multi-Camera configurations - D400](https://dev.intelrealsense.com/docs/multiple-depth-cameras-configuration) 和[px4 Camera Configuration
](https://docs.px4.io/main/en/peripherals/camera.html), 有一些麻烦，因为D435 需要1.8V触发信号

Closed 2023-04-12.

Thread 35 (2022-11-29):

pixhawk4 no longer available

FaboNo, 2022-11-29:
thank you very much for sharing this amazing project (and years of research) with the community
I see that pixhawk4 is sold out almost everywhere so I am wondering if there is any issue with the latest version of pixhawk 6C or CUAV? Indeed in this case, one have to use a difference release of PX4 such px4 fmu v6 for instance

PanNeng-ZJU, 2022-11-30:
We're sorry for this. CUAV V5+works well, and some of the students of this course have tried pixhawk 6C and it turns out fine.

EhrazImam, 2022-11-30:
Hi @PanNeng-ZJU well i tried with cube orange and it works fine as i am also having pixhawk 6C but as soon as i am turning of the magnetometer(as given in the README) i am not getting the /mavros/imu/data. As i can see you mention you have tried pixhawk 6C cane you you just help me with same.
Thankyou

PanNeng-ZJU, 2022-11-30:
@EhrazImam I'm sorry that I didn't try pixhawk 6C on my own, but some of the students did. I guess you can try different version of firmware, like 1.13, and it may work.

EhrazImam, 2022-11-30:
@PanNeng-ZJU I tried it with 1.13.0 master version, 1.13.1, 1.13.2 and i found the same error where i cube orange is working fine in all version.

PanNeng-ZJU, 2022-11-30:
@EhrazImam In that case, I think you can refer to the holybro manufacturer or px4 official for more advice.

EhrazImam, 2022-11-30:
@PanNeng-ZJU Thankyou, yeah i have been trying to ask them but i couldn't find any reply from them, it will be great if i could connect with the students that have tried on pixhawk 6C.

FaboNo, 2022-11-30:
@EhrazImam the orange cube is a pixhawk2 version, you were able to run px fmu v5 on it? I have the black one so I will give it a try
@PanNeng-ZJU I did not see in the README that you need to deactivate the magnetometer - can you tell us why is it necessary?
Thank you very much

EhrazImam, 2022-11-30:
@FaboNo No havent tried with FMU v5 same out of stock so haven't tried

BruceShine, 2022-11-30:
I have successfully run ego-planner with pixhawk 6c. Have you tried daily build QGroundControl to burn firmware?
https://docs.qgroundcontrol.com/master/en/releases/daily_builds.html

EhrazImam, 2022-11-30:
> I have successfully run ego-planner with pixhawk 6c. Have you tried daily build QGroundControl to burn firmware? https://docs.qgroundcontrol.com/master/en/releases/daily_builds.html

Hi yeah i have tried did you change the SYS_MC_EST_GROUP = Q atttitude or you are running it without changing this.

EhrazImam, 2022-12-09:
Hi @BruceShine cane you please clear this issue

BruceShine, 2022-12-14:
> > I have successfully run ego-planner with pixhawk 6c. Have you tried daily build QGroundControl to burn firmware? https://docs.qgroundcontrol.com/master/en/releases/daily_builds.html
>
> Hi yeah i have tried did you change the SYS_MC_EST_GROUP = Q atttitude or you are running it without changing this. And which firmware version you are using. Thankyou

I did not change that parameter. As for firmware, just use the recommended stable version by QGC.

EhrazImam, 2022-12-30:
@FaboNo @BruceShine @PanNeng-ZJU  I am facing running VINS FUSION with Pixhawk 6C as i have run it with Cube Orange and Pixhawk 4 and D435i's IMU and it was running very smoothly.
However i am not sure this is due to Pixhawk 6C's IMU please have a look at IMU.yaml(calibrated with imu_utils).

#Accelerometers
accelerometer_noise_density: 8.7630907909861493e-03   #Noise density (continuous-time)
accelerometer_random_walk:   3.6846874274508294e-04   #Bias random walk

#Gyroscopes
gyroscope_noise_density:     8.9757009701970693e-04  #Noise density (continuous-time)
gyroscope_random_walk:       7.5769383737709901e-06   #Bias random walk

rostopic:                    /mavros/imu/data      #the IMU ROS topic
update_rate:                 200.0     #Hz (for discretization of the values above)

Calibration results
===================
Normalized Residuals
----------------------------
Reprojection error (cam0):     mean 0.3304897901167408, median 0.2200004172986265, std: 0.41110001871708324
Reprojection error (cam1):     mean 0.32047461695261253, median 0.210521224108912, std: 0.40733175830316104
Gyroscope error (imu0):        mean 2.3650272386308853, median 0.900469841552671, std: 3.6080615076365934
Accelerometer error (imu0):    mean 0.8969253003256608, median 0.5084065251567538, std: 1.3295349711772715

Residuals
----------------------------
Reprojection error (cam0) [px]:     mean 0.3304897901167408, median 0.2200004172986265, std: 0.41110001871708324
Reprojection error (cam1) [px]:     mean 0.32047461695261253, median 0.210521224108912, std: 0.40733175830316104
Gyroscope error (imu0) [rad/s]:     mean 0.031485881950145136, median 0.011988059447131917, std: 0.04803454135440456
Accelerometer error (imu0) [m/s^2]: mean 0.11658023498803086, median 0.06608148097807301, std: 0.17280981962307645

Transformation (cam0):
-----------------------
T_ci:  (imu0 to cam0):
[[-0.0011831  -0.99949408 -0.03178334  0.02789416]
 [-0.01458597  0.03179723 -0.99938791  0.00909488]
 [ 0.99989292 -0.00071878 -0.01461621 -0.06212618]
 [ 0.          0.          0.          1.        ]]

T_ic:  (cam0 to imu0):
[[-0.0011831  -0.01458597  0.99989292  0.06228519]
 [-0.99949408  0.03179723 -0.00071878  0.0275462 ]
 [-0.03178334 -0.99938791 -0.01461621  0.00906783]
 [ 0.          0.          0.          1.        ]]

timeshift cam0 to imu0: [s] (t_imu = t_cam + shift)
-0.0016585079261203777

Transformation (cam1):
-----------------------
T_ci:  (imu0 to cam1):
[[-0.0045073  -0.99947521 -0.03207801 -0.02228279]
 [-0.0139655   0.03213812 -0.99938586  0.0090407 ]
 [ 0.99989232 -0.00405655 -0.01410303 -0.06163653]
 [ 0.          0.          0.          1.        ]]

T_ic:  (cam1 to imu0):
[[-0.0045073  -0.0139655   0.99989232  0.06165571]
 [-0.99947521  0.03213812 -0.00405655 -0.02281168]
 [-0.03207801 -0.99938586 -0.01410303  0.0074511 ]
 [ 0.          0.          0.          1.        ]]

timeshift cam1 to imu0: [s] (t_imu = t_cam + shift)
-0.0017732647034794681

Baselines:
----------
Baseline (cam0 to cam1):
[[ 0.99999443  0.00034357 -0.00331956 -0.05038615]
 [-0.00034152  0.99999975  0.00062013 -0.00000612]
 [ 0.00331977 -0.00061899  0.9999943   0.00040233]
 [ 0.          0.          0.          1.        ]]
baseline norm:  0.05038775847016609 [m]

Gravity vector in target coords: [m/s^2]
[ 9.80627198 -0.01036926  0.07311062]

Calibration configuration
=========================

cam0
-----
  Camera model: pinhole
  Focal length: [370.7108040376509, 372.99870767379053]
  Principal point: [319.78661509710616, 239.45619458177592]
  Distortion model: radtan
  Distortion coefficients: [-0.007247130905233888, -0.004773953477251725, -0.0018260889423888547, -0.00011655993921176293]
  Type: aprilgrid
  Tags:
    Rows: 6
    Cols: 6
    Size: 0.022 [m]
    Spacing 0.006599999999999999 [m]

cam1
-----
  Camera model: pinhole
  Focal length: [370.7135602083122, 373.1960137433778]
  Principal point: [321.2458053488056, 239.32180866261118]
  Distortion model: radtan
  Distortion coefficients: [-0.00549041557346843, -0.004442582242381625, -0.002207008976176078, -9.093312682821986e-06]
  Type: aprilgrid
  Tags:
    Rows: 6
    Cols: 6
    Size: 0.022 [m]
    Spacing 0.006599999999999999 [m]

IMU configuration
=================

IMU0:
 ----------------------------
  Model: calibrated
  Update rate: 220.0
  Accelerometer:
    Noise density: 0.00876309079098615
    Noise density (discrete): 0.12997764133278683
    Random walk: 0.00036846874274508294
  Gyroscope:
    Noise density: 0.0008975700970197069
    Noise density (discrete): 0.013313115991159715
    Random walk: 7.57693837377099e-06
  T_i_b
    [[1. 0. 0. 0.]
     [0. 1. 0. 0.]
     [0. 0. 1. 0.]
     [0. 0. 0. 1.]]
  time offset with respect to IMU0: 0.0 [s]

As soon i am taking yaw it's drifting a lot.
Thankyou

Closed 2022-11-30.

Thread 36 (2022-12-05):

关于控制器部分的问题

pugummy, 2022-12-05:
您好！首先感谢您的分享！
请问px4ctrl里面控制器设计部分有没有参考文献呢？不是很明白控制器输出的姿态的计算方法。^_^

dongdongbh, 2023-01-13:
同疑问，不是很理解这两行

https://github.com/ZJU-FAST-Lab/Fast-Drone-250/blob/8ff64274b161bb829653faf5946656658e7e2c9f/src/realflight_modules/px4ctrl/src/controller.cpp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

是一种参考重力向量（认为机体加速度较小）对姿态的粗略估算吗？

FaboNo, 2023-01-31:
@dongdongbh the equations are coming from which paper?
方程式来自哪篇论文？

Nikanbaturu, 2023-02-15:
@dongdongbh 您好！请问可以把controller理解为位置控制器吗？而且没太看懂对debug_msg_赋值的意义，是为了存储计算得到的期望值将其作为内级控制器的输入吗？

dongdongbh, 2023-02-15:
debug_msg_只是为了debug方便而发布的topic，最终油门和姿态给了飞控，控制是位置和速度的P控制外加加速度前馈给到姿态控制器做串级

Nikanbaturu, 2023-02-16:
@dongdongbh 感谢您的回答，那controller这部分的位置控制算法是否可以替换成其他的呢？

dongdongbh, 2023-02-16:
可以

dongdongbh, 2023-02-22:
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
Finally understand it by reading their PPT

FaboNo, 2023-02-22:
@dongdongbh oh very interesting, where did you find the ppt?

dongdongbh, 2023-02-23:
Here is a [video](https://www.bilibili.com/video/BV1Jq4y1T7QD/?spm_id_from=333.337.search-card.all.click) with this ppt talking about these things, but in Chinese.

karjalv, 2023-02-27:
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

@dongdongbh Have you found any reason for this division with `rho2_` ? I've been wondering the same thing.

bulingda, 2023-03-24:
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

Hello, do you understand the meaning of this formula?

Closed 2023-04-12.

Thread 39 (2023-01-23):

Few questions about the firmware release and Pixhawk orientation

FaboNo, 2023-01-23:
Dear All,

As mentioned in a previous message, instead of a pixhawk 4 mini (no more available), I had to purchase a Pixhawk 6x mini.
In your READ.ME you mentioned that we have to use the v1.11.0 but this version does not support the Pixhawk 6x (starting with v1.12.0). So the question is can you tell us why the v1.13 is not suitable, and is it still not suitable with the new hardware?

Regarding the assembling, we have to set up the pixhawk "perpendicular" to the front face of the drone. Why do we have to do this? Because of VINS? Because when we are testing the drone with the pixhawk only and the AT9S PRO, if the pilot wants to go forward, the drone will move sideway
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

Thank you very much for answering the question and helping us to reproduce what you do in your lab!

PanNeng-ZJU, 2023-04-12:
1. we were having some trouble of unstable measurement of VIO with the 1.13.0 firmware, but I think you can give it a try in the pixhawk 6c.
2. The reason why we set up the pixhawk "perpendicular" to the front face of the drone, is that it's more suitable for installation. As long as the orientation of the flight controller is configured properly in the calibration part in the QGC, you can install the flight controller any way you want.

EhrazImam, 2023-08-30:
@FaboNo hope you are doing well were you able to run on pixhawk 6x

EhrazImam, 2023-08-30:
Any other hardware you have used

For 200 hz create a file etc/extras.txt and add  mavlink stream -d /dev/ttyS0 -s HIGHRES_IMU -r 200
mavlink stream -d /dev/ttyS0 -s ODOMETRY -r 200

FaboNo, 2023-09-03:
@EhrazImam yes it is working by doing this (I saw it in on issue):
roslaunch mavros px4.launch &sleep 10;
rosrun mavros mavcmd long 511 105 4550 0 0 0 0 0 &sleep 1;
echo "/mavros/imu/data_raw to 200Hz"
rosrun mavros mavcmd long 511 31  4550 0 0 0 0 0 &sleep 1;
echo "/mavros/imu/data to 200Hz"

Closed 2023-04-12.

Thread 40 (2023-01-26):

Using ZED camera instead of D435

EhrazImam, 2023-01-26:
Hi @ZhepeiWang Hope you are doing well I want to use ZED camera instead of d435, As i am able to run it with D435 i want know what parameters i need to change apart from depth topic and intrinsic values.
Do i need to change something over here https://github.com/ZJU-FAST-Lab/Fast-Drone-250/blob/8ff64274b161bb829653faf5946656658e7e2c9f/src/planner/plan_manage/launch/advanced_param_exp.xml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

PanNeng-ZJU, 2023-04-12:
Basically, you just need to change the depth topic, and the intrinsic values. The _depth_filter_maxdist_ param can be changed according to the maximum sensing range of your sensor.

Closed 2023-04-12.

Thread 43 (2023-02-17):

ego planner die when launched

FPSychotic, 2023-02-17:
roslaunch ego_planner single_run_in_exp.launch
... logging to /home/oem/.ros/log/9f347834-aeb9-11ed-927f-9304ded37c71/roslaunch-ihexa-53043.log
Checking log directory for disk usage. This may take a while.
Press Ctrl-C to interrupt
Done checking log file disk usage. Usage is <1GB.

started roslaunch server http://ihexa:42275/

SUMMARY
========

PARAMETERS
 * /drone_0_ego_planner_node/bspline/limit_acc: 2.0
 * /drone_0_ego_planner_node/bspline/limit_ratio: 1.1
 * /drone_0_ego_planner_node/bspline/limit_vel: 0.25
 * /drone_0_ego_planner_node/fsm/emergency_time: 1.0
 * /drone_0_ego_planner_node/fsm/fail_safe: True
 * /drone_0_ego_planner_node/fsm/flight_type: 1
 * /drone_0_ego_planner_node/fsm/planning_horizon: 6.0
 * /drone_0_ego_planner_node/fsm/planning_horizon_time: 3.0
 * /drone_0_ego_planner_node/fsm/realworld_experiment: True
 * /drone_0_ego_planner_node/fsm/thresh_no_replan_meter: 1.0
 * /drone_0_ego_planner_node/fsm/thresh_replan_time: 1.0
 * /drone_0_ego_planner_node/fsm/waypoint0_x: 15.0
 * /drone_0_ego_planner_node/fsm/waypoint0_y: 0.0
 * /drone_0_ego_planner_node/fsm/waypoint0_z: 1.0
 * /drone_0_ego_planner_node/fsm/waypoint1_x: 0.0
 * /drone_0_ego_planner_node/fsm/waypoint1_y: 0.0
 * /drone_0_ego_planner_node/fsm/waypoint1_z: 1.0
 * /drone_0_ego_planner_node/fsm/waypoint2_x: 15.0
 * /drone_0_ego_planner_node/fsm/waypoint2_y: 0.0
 * /drone_0_ego_planner_node/fsm/waypoint2_z: 1.0
 * /drone_0_ego_planner_node/fsm/waypoint3_x: 0.0
 * /drone_0_ego_planner_node/fsm/waypoint3_y: 0.0
 * /drone_0_ego_planner_node/fsm/waypoint3_z: 1.0
 * /drone_0_ego_planner_node/fsm/waypoint4_x: 15.0
 * /drone_0_ego_planner_node/fsm/waypoint4_y: 0.0
 * /drone_0_ego_planner_node/fsm/waypoint4_z: 1.0
 * /drone_0_ego_planner_node/fsm/waypoint_num: 1
 * /drone_0_ego_planner_node/grid_map/cx: 162.2635345458984
 * /drone_0_ego_planner_node/grid_map/cy: 117.3401031494141
 * /drone_0_ego_planner_node/grid_map/depth_filter_margin: 2
 * /drone_0_ego_planner_node/grid_map/depth_filter_maxdist: 5.0
 * /drone_0_ego_planner_node/grid_map/depth_filter_mindist: 0.2
 * /drone_0_ego_planner_node/grid_map/depth_filter_tolerance: 0.15
 * /drone_0_ego_planner_node/grid_map/frame_id: world
 * /drone_0_ego_planner_node/grid_map/fx: 307.8522033691406
 * /drone_0_ego_planner_node/grid_map/fy: 310.60693359375
 * /drone_0_ego_planner_node/grid_map/ground_height: -0.01
 * /drone_0_ego_planner_node/grid_map/k_depth_scaling_factor: 1000.0
 * /drone_0_ego_planner_node/grid_map/local_map_margin: 10
 * /drone_0_ego_planner_node/grid_map/local_update_range_x: 5.5
 * /drone_0_ego_planner_node/grid_map/local_update_range_y: 5.5
 * /drone_0_ego_planner_node/grid_map/local_update_range_z: 4.5
 * /drone_0_ego_planner_node/grid_map/map_size_x: 50
 * /drone_0_ego_planner_node/grid_map/map_size_y: 50
 * /drone_0_ego_planner_node/grid_map/map_size_z: 5.0
 * /drone_0_ego_planner_node/grid_map/max_ray_length: 5.0
 * /drone_0_ego_planner_node/grid_map/min_ray_length: 0.3
 * /drone_0_ego_planner_node/grid_map/obstacles_inflation: 0.5
 * /drone_0_ego_planner_node/grid_map/p_hit: 0.65
 * /drone_0_ego_planner_node/grid_map/p_max: 0.9
 * /drone_0_ego_planner_node/grid_map/p_min: 0.12
 * /drone_0_ego_planner_node/grid_map/p_miss: 0.35
 * /drone_0_ego_planner_node/grid_map/p_occ: 0.8
 * /drone_0_ego_planner_node/grid_map/pose_type: 2
 * /drone_0_ego_planner_node/grid_map/resolution: 0.2
 * /drone_0_ego_planner_node/grid_map/show_occ_time: False
 * /drone_0_ego_planner_node/grid_map/skip_pixel: 2
 * /drone_0_ego_planner_node/grid_map/use_depth_filter: True
 * /drone_0_ego_planner_node/grid_map/visualization_truncate_height: 1.8
 * /drone_0_ego_planner_node/manager/control_points_distance: 0.4
 * /drone_0_ego_planner_node/manager/drone_id: 0
 * /drone_0_ego_planner_node/manager/feasibility_tolerance: 0.05
 * /drone_0_ego_planner_node/manager/max_acc: 2.0
 * /drone_0_ego_planner_node/manager/max_jerk: 4.0
 * /drone_0_ego_planner_node/manager/max_vel: 0.25
 * /drone_0_ego_planner_node/manager/planning_horizon: 6.0
 * /drone_0_ego_planner_node/manager/use_distinctive_trajs: False
 * /drone_0_ego_planner_node/optimization/dist0: 0.5
 * /drone_0_ego_planner_node/optimization/lambda_collision: 0.5
 * /drone_0_ego_planner_node/optimization/lambda_feasibility: 0.1
 * /drone_0_ego_planner_node/optimization/lambda_fitness: 1.0
 * /drone_0_ego_planner_node/optimization/lambda_smooth: 1.0
 * /drone_0_ego_planner_node/optimization/max_acc: 2.0
 * /drone_0_ego_planner_node/optimization/max_vel: 0.25
 * /drone_0_ego_planner_node/optimization/swarm_clearance: 0.5
 * /drone_0_ego_planner_node/prediction/lambda: 1.0
 * /drone_0_ego_planner_node/prediction/obj_num: 10
 * /drone_0_ego_planner_node/prediction/predict_rate: 1.0
 * /drone_0_traj_server/traj_server/time_forward: 1.0
 * /rosdistro: noetic
 * /rosversion: 1.15.15

NODES
  /
    drone_0_ego_planner_node (ego_planner/ego_planner_node)
    drone_0_traj_server (ego_planner/traj_server)

ROS_MASTER_URI=http://localhost:11311

process[drone_0_ego_planner_node-1]: started with pid [53178]
process[drone_0_traj_server-2]: started with pid [53179]
hit: 0.619039
miss: -0.619039
min log: -1.99243
max: 2.19722
thresh log: 1.38629
[FSM]: from INIT to WAIT_TARGET
[ WARN] [1676641698.037088225]: [Traj server]: ready.
[drone_0_ego_planner_node-1] process has died [pid 53178, exit code -11, cmd /home/oem/ihexa_ws/devel/lib/ego_planner/ego_planner_node ~odom_world:=/vins_fusion/imu_propagate ~planning/bspline:=/drone_0_planning/bspline ~planning/data_display:=/drone_0_planning/data_display ~planning/broadcast_bspline_from_planner:=/broadcast_bspline ~planning/broadcast_bspline_to_planner:=/broadcast_bspline ~grid_map/odom:=/vins_fusion/imu_propagate ~grid_map/cloud:=nouse2 ~grid_map/pose:=nouse1 ~grid_map/depth:=/camera/depth/image_rect_raw __name:=drone_0_ego_planner_node __log:=/home/oem/.ros/log/9f347834-aeb9-11ed-927f-9304ded37c71/drone_0_ego_planner_node-1.log].
log file: /home/oem/.ros/log/9f347834-aeb9-11ed-927f-9304ded37c71/drone_0_ego_planner_node-1*.log
^C[drone_0_traj_server-2] killing on exit
shutting down processing monitor...
... shutting down processing monitor complete
done

FPSychotic, 2023-02-18:
I noted if I first launch the node and later vins, it will not crash immediately, will survive a time, and depending the settings , sometimes will last quite more, could CPU load, or IMU with bad sychro ?

2500035435, 2023-03-29:
I also met the same problem. Have you found the solution？

PanNeng-ZJU, 2023-04-12:
The mostly likely reason is that your VIO flies away, and the position is beyond the range of the map size set up of the planner, and it dies.

Closed 2023-04-12.

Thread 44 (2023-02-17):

Drone detect id=1 instead =0

FPSychotic, 2023-02-17:
In this drone detect launch make reference to ID=1 but every other launch refer ID as 0, is that right?

<launch>
  <arg name="my_id" value="1"/>
  <arg name="odom_topic" value="/vins_fusion/imu_propagate"/>

  <!-- Launch ROS Package Template Node -->
  <node pkg="drone_detect" type="drone_detect" name="test_drone_detect" output="screen">
    <rosparam command="load" file="$(find drone_detect)/config/camera.yaml" />
    <rosparam command="load" file="$(find drone_detect)/config/default.yaml"/>
    <param name="my_id"      value="$(arg my_id)" />
    <param name="debug_flag" value="false" />
    <remap from="~odometry"   to="$(arg odom_topic)"/>
    <remap from="~depth" to="/camera/depth/image_rect_raw"/>
    <!-- <remap from="~camera_pose" to="/drone_$(arg my_id)_pcl_render_node/camera_pose"/> -->

    <!-- <remap from="~drone0" to="/drone_0_$(arg odom_topic)"/>
    <remap from="~drone1" to="/drone_1_$(arg odom_topic)"/>
    <remap from="~drone2" to="/drone_2_$(arg odom_topic)"/> -->

    <!-- <remap from="~drone1" to="/test/dynamic0_odom"/> -->
    <!-- <remap from="~drone2" to="/test/dynamic1_odom"/> -->

  </node>

</launch>

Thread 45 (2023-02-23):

PX4 Cntrl

EhrazImam, 2023-02-23:
@bigsuperZZZX @ZhepeiWang As you can see over here https://github.com/ZJU-FAST-Lab/Fast-Drone-250/issues/33#issuecomment-1331634422
I want to know if we are using VIO then why we need mavros/imu/data as far i know that mavros/imu/data gives us acc,gyro and orientation and where as /mavros/imu/data_raw we only get acc and gyro.
If you are flying over VIO, why do you need the magnetometer?
Thankyou

bigsuperZZZX, 2023-03-16:
See https://github.com/ZJU-FAST-Lab/ego-planner/issues/68#issuecomment-1471883970

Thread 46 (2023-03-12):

vins齐次变换矩阵填法

qllokirin, 2023-03-12:
感谢您地项目！
1 视频中飞控和相机有一个90度的差值，但是在我的飞机上二者都朝前，请问这种情况下旋转矩阵应该怎么写？
2 我有学习到旋转矩阵计算方法，但是我不清楚imu和相机的坐标系朝向（网上也众说纷纭），请问可以告知一下吗
3 我想确认一下 齐次变换矩阵的最后一列的xyz是以imu为原点前x左y右z来计算相机的位置吗
这真的很困扰我  期待您的解答

PanNeng-ZJU, 2023-04-12:
1. 与飞控摆放位置无关，保持默认即可
2. 前x左y上z
3.  前x左y上z

qllokirin, 2023-04-12:
非常感谢

Closed 2023-04-12.

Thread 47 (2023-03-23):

跑 sh shfiles/rspx4.sh时候，请问这个opencv的问题怎么解决

WWWWYYYYAAAA, 2023-03-23:
erminate called after throwing an instance of 'cv::Exception'
  what():  OpenCV(4.2.0) /home/wya/opencv4/opencv/modules/video/src/lkpyramid.cpp:1257: error: (-215:Assertion failed) maxLevel >= 0 && winSize.width > 2 && winSize.height > 2 in function 'calc'

[vins_fusion-1] process has died [pid 24975, exit code -6, cmd /home/wya/fastdrone/ego-planner-pure/devel/lib/vins/vins_node /home/wya/fastdrone/ego-planner-pure/src/realflight_modules/VINS-Fusion/vins_estimator/../config/fast_drone_250.yaml __name:=vins_fusion __log:=/home/wya/.ros/log/8a6bf5de-c968-11ed-b007-eb26846a03d9/vins_fusion-1.log].
log file: /home/wya/.ros/log/8a6bf5de-c968-11ed-b007-eb26846a03d9/vins_fusion-1*.log
all processes on machine have died, roslaunch will exit
shutting down processing monitor...
... shutting down processing monitor complete

WWWWYYYYAAAA, 2023-04-08:
change opencv version to 3..44

Closed 2023-04-08.

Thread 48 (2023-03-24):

有一处不理解的代码

bulingda, 2023-03-24:
src/realflight_modules/px4ctrl/src/input.cpp 113 行
bool RC_Data_t::check_centered()
{
    bool centered = abs(ch[0]) < 1e-5 && abs(ch[0]) < 1e-5 && abs(ch[0]) < 1e-5 && abs(ch[0]) < 1e-5;
    return centered;
}
你好，想问一下，这里所有都是ch[0]是什么意思呢？

PanNeng-ZJU, 2023-04-12:
不好意思，这是一处bug，应为ch[0~3]

Closed 2023-04-12.

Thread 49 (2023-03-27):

关于hover percentage的print value的问题

BizzareNathan, 2023-03-27:
视频中提到可以通过修改ctrl_param_fpv.yaml文件中的thrust_model：print value设置为true来打印hover percentage，但是在实际使用中开启了，以后并没有在实际的终端界面中看见这个参数的打印，只能在开始时看见一个ROS_WARN("You should disable \"print_value\" if you are in regular usage.");
请问可以提供这个的正确修改方法或者是其他可以来调整这个参数的方法吗？

PanNeng-ZJU, 2023-04-12:
不好意思，这个功能暂时还没有，你可以去代码相应位置自行打印一下

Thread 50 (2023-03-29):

agx xavier运行ego_planner出现问题

2500035435, 2023-03-29:
很感激fastlab团队做出的贡献，最近也在结合你们的视频教程弄自己的东西，我用的是jetson AGX Xavier，CUAV V5+固件版本1.11，vins-fusion替换成了vins-fusion-gpu版本，运行时GPU有20%多的使用率。问题出现在运行vins之后再运行ego_planner，终端会出现报错
[drone_0_ego_planner_node-2] process has died [pid 935, exit code -11, cmd /home/hyy/catkin_ws/devel/lib/ego_planner/ego_planner_node ~odom_world:=/vins_fusion/imu_propagate ~planning/bspline:=/drone_0_planning/bspline ~planning/data_display:=/drone_0_planning/data_display ~planning/broadcast_bspline_from_planner:=/broadcast_bspline ~planning/broadcast_bspline_to_planner:=/broadcast_bspline ~grid_map/odom:=/vins_fusion/imu_propagate ~grid_map/cloud:=nouse2 ~grid_map/pose:=nouse1 ~grid_map/depth:=/camera/depth/image_rect_raw __name:=drone_0_ego_planner_node __log:=/home/hyy/.ros/log/aacab844-ce0c-11ed-89c8-3413e862af5c/drone_0_ego_planner_node-2.log].
log file: /home/hyy/.ros/log/aacab844-ce0c-11ed-89c8-3413e862af5c/drone_0_ego_planner_node-2*.log
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
单独运行ego的话并不会出现报错，或者先运行ego再运行vins，过了一段时间才会出现报错。想请问一下是什么原因？有什么解决办法吗？

otis-XJY, 2023-12-07:
> 很感激fastlab团队做出的贡献，最近也在结合你们的视频教程弄自己的东西，我用的是jetson AGX Xavier，CUAV V5+固件版本1.11，vins-fusion替换成了vins-fusion-gpu版本，运行时GPU有20%多的使用率。问题出现在运行vins之后再运行ego_planner，终端会出现报错 [drone_0_ego_planner_node-2] process has died [pid 935, exit code -11, cmd /home/hyy/catkin_ws/devel/lib/ego_planner/ego_planner_node ~odom_world:=/vins_fusion/imu_propagate ~planning/bspline:=/drone_0_planning/bspline ~planning/data_display:=/drone_0_planning/data_display ~planning/broadcast_bspline_from_planner:=/broadcast_bspline ~planning/broadcast_bspline_to_planner:=/broadcast_bspline ~grid_map/odom:=/vins_fusion/imu_propagate ~grid_map/cloud:=nouse2 ~grid_map/pose:=nouse1 ~grid_map/depth:=/camera/depth/image_rect_raw __name:=drone_0_ego_planner_node __log:=/home/hyy/.ros/log/aacab844-ce0c-11ed-89c8-3413e862af5c/drone_0_ego_planner_node-2.log]. log file: /home/hyy/.ros/log/aacab844-ce0c-11ed-89c8-3413e862af5c/drone_0_ego_planner_node-2*.log 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 单独运行ego的话并不会出现报错，或者先运行ego再运行vins，过了一段时间才会出现报错。想请问一下是什么原因？有什么解决办法吗？

请问您是怎么解决的呢

Closed 2023-04-17.

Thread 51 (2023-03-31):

悬停的时候会往下掉

LChen-99, 2023-03-31:
请问在悬停的时候飞机一段时间会往下掉，imu的震动不大。不知道是油门估计不准确导致的还是PID没调好。

PanNeng-ZJU, 2023-04-12:
可以更详细地描述一下吗，最好附上视频

LiPengfei0805, 2025-05-28:
本人实验中也遇到过该现象，后续发现是因为px4ctrl中ctrl_param_fpv.yaml文件下的Kv2参数过大，最终会导致迭代计算出的悬停期望高度不断变小，无人机不断下降。可在代码中添加期望高度日志查看期望高度是否不断变小，以确认是否是该原因

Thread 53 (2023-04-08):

px4ctrl yaw bug

Poaos, 2023-04-08:
您好，我最近在使用px4ctrl控制四旋翼时遇到了问题:
目前采用t265定位，px4ctrl订阅 /mavros/local_position/odom和/mavros/imu/data，只不过他们都频率都没有高于100hz。不知道是否影响。

px4ctrl控制无人机自动起飞并悬停后，遥控器控制四旋翼的油门，roll，pitch这些都正常，但是控制yaw时，如果yaw角度变化大于100度（大概），无人机就会开始圆周运动，并且是半径越转越大那种（最后会失速往一个方向炸鸡）。config文件中的参数我基本上都已经对应修改过了，那个kp kv也尝试改小过，都是一样的效果。当然，如果我在上述情况下立马切出offboard，飞机就能够一下子稳定住。（过程中/mavros/local_position/odom还是正常的，没有飘）

这个问题是我在飞egoplanner的时候，先设定目标点（3，0，1），正常飞过去，再设定（2，0，1），无人机转向后就会直接往某个方向炸鸡，多次排查后发现的。我目前判断问题应该是px4ctrl本身的，因为纯t265的时候，使用px4自己的位置控制没有出现过这些情况。不知道您是否遇到过这种情况，或者有大概的问题解决思路?

PanNeng-ZJU, 2023-04-12:
t265的速度反馈有问题，如果要用它做里程计的话，需要融合imu数据，你这种类似情况我也遇到过。

EhrazImam, 2023-04-13:
Hi @PanNeng-ZJU even i faced the exact same problem and i am using openvins and vin-fusion where the pixhawk imu and the problem lies same.

PanNeng-ZJU, 2023-04-13:
@EhrazImam @Poaos 问题在于你们使用的里程计的速度反馈有问题，比较正确的解决办法是，将里程计与IMU进行ekf融合，获得一个相对正确的速度估计；相对妥协的办法是，直接在px4ctrl中速度误差反馈的位置，直接把它关掉，但这会导致位置跟踪误差变大

Ding-Guo, 2023-04-20:
我用仿真软件调px_ctrl也遇到了一样的问题

Ding-Guo, 2023-04-24:
我在仿真里面已经解决了我遇到的问题，问题确实如大佬所说是速度反馈出现了问题，对于我的情况是因为反馈的速度的坐标系是相对于机体坐标系，需要对速度做一个旋转变换。

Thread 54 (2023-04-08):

Question about external yaw estimator

dssdyx, 2023-04-08:
Thank you for such a great project. I have read carefully of your work. But I want to ask the question that  if the running env is indoor,which may be disturbed for Px4 FCU inner magnetometer,could the attitude controller still keep robust ?
   As I know, you don't use GPS module, meaning your drone only has one magenetometer inside the Pixhawk 4 mini. This magenetometer is not reliable because it's close to many wires, affected by current magnetic field. Here, the FCU orientation is computed by imu and magenetometer.
  Indoor env is not usually clean. It may exist some electronic devices resulting in magenetometer failure. Then the FCU orientation, specially yaw estimation may not be stable.
   So, is it necessary to make VIO yaw estimation take part in FCU Fusion?
   Hope for your answer. Thank you so much!

PanNeng-ZJU, 2023-04-12:
The magenetometer is not used in this project, and the yaw is estimated by the integration of imu and VIO.

Closed 2023-04-12.

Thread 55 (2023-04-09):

无人机自动起飞失败

Nikanbaturu, 2023-04-09:
按照教程，完成VINS标定后进行自动起飞悬停实验。下发命令后，无人机在自动起飞过程中，一开始起飞到了一个很低的位置，观察来看好像是无人机因为过中飞不起来，随后无人机急剧加速失控，并上升到了很高的位置，但echo /vins_fusion/imu_propogate vins并没有漂，请问这是什么情况导致的？
Ps：
    1.  我的无人机飞控选用的是雷迅V5+
    2.  由于使用的飞控不一样，并且我自行安装了防护圈，飞机重量比视频教程中的要大，约重1.5kg
    3. 起飞后悬停高度设置成了 0.6m，而不是默认的1.0m

PanNeng-ZJU, 2023-04-12:
建议尝试加高config文件里的hover_percentage值到你的实际悬停油门再测试

eleboss, 2023-06-07:
hi pan博您好，
我也遇到了类似的问题，我的整机是S500的框架，起飞的hover percent根据遥控器上油门的数值设置到大概35%左右，无人机缓慢起飞到设定的0.6m时候能够稳定在那个位置，然后过一会就会突然加速冲刺，向上飞，每次出现这种情况我都是直接切手动降落，为什么会这样呢？

eleboss, 2023-06-07:
update，
似乎无人机并没办法稳定到固定的高度，我的无人机晃得很厉害，在设定点附近震荡

eleboss, 2023-06-08:
update,
我尝试用比较小的位置p，和比较大的速度p，貌似都没办法很好的定住。整个飞机就是在高度位置附近震荡，是不是控制器没有微分项导致的呢？

PanNeng-ZJU, 2023-06-08:
请查看一下/mavros/imu/data话题的数据，因为你更换了机架，如果IMU的震动噪声很大，VIO是会很不稳定，从而导致你现在的问题，一般在噪声在+-2以内比较理想 @eleboss

eleboss, 2023-06-08:
@PanNeng-ZJU 感谢回复。我用工具查看了一下飞机在手动模式下的IMU噪声情况，我手动打开螺旋桨，然后把油门推到35%（起飞临界），然后记录了IMU的采样结果。这样一个噪声情况算比较严重的吗？
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

eleboss, 2023-06-09:
@PanNeng-ZJU  感谢回复，我更换了一套新的动力系统，噪声能到+-3左右。正在测试，似乎效果明显好转。不过可能是因为控制器PD参数的原因，每次起飞有些许超调，定点依旧有困难。pan博有在大轴距调试参数的经验吗？或者有什么可以分享的经验吗？

eleboss, 2023-06-12:
update,
不是噪声的问题，没用dshot，导致控制缓慢。改了dshot之后就好了。

Closed 2023-06-13.

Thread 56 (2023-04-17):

Collision Prevention with PX4

bhaskar-glitch, 2023-04-17:
Hi,
I want to implement collision prevention in my drone using your PX4 control.
I am using Pixhawk cube with my own depth camera.

Please help me with the steps to implement the same.

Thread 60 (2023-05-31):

关于实际飞行时数据转换的问题

cheslee-z, 2023-05-31:
你好，请问vins-fusion输出的位姿是怎么转换为飞控所需要的定位信息的，我没有找到对应的topic映射关系；此外，d435i相机是如何实现同时输出双目图像和深度图像的呢，我编译该项目的源码后启动realsense_ros节点，用rqt_image_view查看双目图像都具有光点。我知道ego-planner改进了realsense-ros驱动，但是在issue里也提到那个版本过时了，那这个仓库下用的就是原始的版本吗

2500035435, 2023-06-06:
双目图像有光点应该是结构光没关掉吧？此外，d435i的双目和深度图像输出可以修改rs_camera.launch文件，
"enable_depth"设为true输出深度图像，"enable_infra1"和"enable_infra2"设为true输出双目话题。

cheslee-z, 2023-06-06:
> 双目图像有光点应该是结构光没关掉吧？此外，d435i的双目和深度图像输出可以修改rs_camera.launch文件， "enable_depth"设为true输出深度图像，"enable_infra1"和"enable_infra2"设为true输出双目话题。

直接把结构光关掉会被深度图的成像质量有影响吧

Joosoo1, 2023-06-21:
最好还是关掉，要不然vins会很飘

cheslee-z, 2023-06-21:
> 最好还是关掉，要不然vins会很飘

我现在已经关掉了，但是规划必须得用深度图，这怎么办呢

Joosoo1, 2023-06-21:
不用结构光的话，在环境中多布置一点特征点比较多的物品，依靠双目输出的深度图用来规划勉强够用，飞ego是没问题的

FaboNo, 2023-09-16:
@cheslee-z @Joosoo1 Can you tell me how did you turn off the emitter (lumière structurée) ?
你能告诉我你是如何关闭发射器（lumière structurée）的吗？

Joosoo1, 2024-04-08:
> @cheslee-z @Joosoo1 Can you tell me how did you turn off the emitter (lumière structurée) ? 你能告诉我你是如何关闭发射器（lumière structurée）的吗？

我是直接用黑胶带遮住结构光的

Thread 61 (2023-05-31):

[vins_fusion-2] process has died [pid 23052, exit code -11

snapback0, 2023-05-31:
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
请问这种问题如何解决？
平台：jetson nano
系统：ubuntu18.04
编译Fast-drone-250没问题

snapback0, 2023-06-01:
已解决，安装opencv3.2.0，将find_package(OpenCV 4 REQUIRED)改成find_package(OpenCV 3.2.0 REQUIRED)
再重新编译一次就可以了

Closed 2023-06-08.

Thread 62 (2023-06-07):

你好，请问有关于px4ctrl的参考文献吗？想学习一下它的理论知识

summerandautum, 2023-06-07:
想请问一下px4ctrl参考了那些文献？谢谢！

XXLiu-HNU, 2024-06-11:
【无人机系统 - 高飞组超全讲解！2021ROS暑期学校 第五天精剪回放】 https://www.bilibili.com/video/BV1Jq4y1T7QD/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
参考控制部分的讲解，根据无人机的动力学模型使用PID进行控制

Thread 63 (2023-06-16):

record.sh 文件中最后一行是否多了一个“\” ?

Biude, 2023-06-16:
[ INFO] [1686912190.511128333]: Subscribing to /camera/infra1/image_rect_raw
[ INFO] [1686912190.512702355]: Subscribing to /drone_0_ego_planner_node/goal_point
[ INFO] [1686912190.513699049]: Subscribing to /drone_0_ego_planner_node/grid_map/occupancy_inflate
[ INFO] [1686912190.514698569]: Subscribing to /drone_0_ego_planner_node/init_list
[ INFO] [1686912190.516005986]: Subscribing to /drone_0_ego_planner_node/optimal_list
[ INFO] [1686912190.517788915]: Subscribing to /drone_0_odom_visualization/path
[ INFO] [1686912190.518836154]: Subscribing to /drone_0_odom_visualization/robot
[ INFO] [1686912190.519707753]: Subscribing to /ego_planner_node/a_star_list
[ INFO] [1686912190.520515342]: Subscribing to /ego_planner_node/global_list
[ INFO] [1686912190.521363340]: Subscribing to /position_cmd
[ INFO] [1686912190.522285830]: Subscribing to /vins_fusion/odometry
[ INFO] [1686912190.523258407]: Subscribing to /vins_fusion/path
[ INFO] [1686912190.524125354]: Subscribing to \
terminate called after throwing an instance of 'ros::InvalidNameException'
  what():  Character [\] is not valid as the first character in Graph Resource Name [\].  Valid characters are a-z, A-Z, / and in some cases ~.

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

EGOIST5, 2023-08-08:
是的,最后的那个\去掉就好了

Biude, 2023-08-08:
忘记关了，应该就是这个原因了。影响不大

Closed 2023-08-08.

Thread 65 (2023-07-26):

VINS飘一直未找到原因

EGOIST5, 2023-07-26:
使用的无人机是JCV-600，相机为D435i，机载电脑为jetson xavier nx，
已将VINS修改为GPU版本，即使用https://github.com/pjrambo/VINS-Fusion-gpu这里的文件替换原来的vins-fusion文件夹，并且在其中添加了相应的fast-drone-250.yaml、left.yaml、right.yaml并替换了原来的vins_rviz_config.rviz，并在fast-drone-250.yaml增加了相应的使用GPU参数，其余未做替换。并仿造ego_planner_swarm项目中将相应的CMakeList.txt内容修改set(ENABLE_CUDA true)及 set(CUDA_NVCC_FLAGS
      -gencode arch=compute_72,code=sm_72;
    )
结构光也已经关闭。
但是无人机即使放在远处，VINS显示的position也将不断增加，seq达到六七千的时候x和y可能达到几十，甚至上百，一直未找到相应的原因，之后按照相应的操作去替换相应的矩阵参数，也未得到改善，并且这几次标定发现vins_output/extrinsic_parameter.txt里的内容一直不变。

otis-XJY, 2023-11-10:
我也使用同样的机载电脑和相机，请问是如何解决的呢

2874160799, 2024-07-15:
请问如何解决的呢？

EGOIST5, 2024-07-15:
我当时是矩阵参数不够准确，替换到更准确的矩阵参数后，就不会飘了

2874160799, 2024-07-15:
> 我当时是矩阵参数不够准确，替换到更准确的矩阵参数后，就不会飘了

是外参和内参的标定矩阵吗

EGOIST5, 2024-07-15:
是的

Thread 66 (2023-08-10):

6c mini 提高IMU发布频率 原命令失效

Zhangyucong0210, 2023-08-10:
[第四章第二步](https://github.com/ZJU-FAST-Lab/Fast-Drone-250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)中，写入的命令应该加入一行，最后文件内容应该为
```bash
mavlink start -d /dev/ttyACM0 -b 921600
mavlink stream -d /dev/ttyACM0 -s ATTITUDE_QUATERNION -r 200
mavlink stream -d /dev/ttyACM0 -s HIGHRES_IMU -r 200
```

FRO4TEN, 2023-08-28:
>

同为6cmini 依次更改后仍无法提高imu频率，需要在mavros运行后执行
rosrun mavros mavcmd long 511 105 5000 0 0 0 0 0 & sleep 1;
rosrun mavros mavcmd long 511 31 5000 0 0 0 0 0 & sleep 1;
才可以将发布频率提高至170hz左右
p.s. 固件版本为1.13.3

enord-co, 2023-08-29:
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

Dear @Zhangyucong0210 even i am trying to run with 6c mini, Was it working fine with the ego planner

FRO4TEN, 2023-09-02:
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

可以正常使用

enord-co, 2023-09-02:
@FRO4TEN 感谢您的回复，您在 6c mini 上尝试过此存储库吗

FRO4TEN, 2023-09-09:
> @FRO4TEN 感谢您的回复，您在 6c mini 上尝试过此存储库吗

我目前使用的就是6cmini

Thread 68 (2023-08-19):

RLException: arg 'drone_id' is not defined.

Ultramarine1939-syujie, 2023-08-19:
Everytime I reboot my machine,the error shall occur and I can't test this program
```
WARNING: disk usage in log directory [/home/ubuntu/.ros/log] is over 1GB.
It's recommended that you use the 'rosclean' command.

RLException: arg 'drone_id' is not defined.

Arg xml is <arg name="drone_id" value="$(arg drone_id)"/>
The traceback for the exception was written to the log file

```

Closed 2023-08-19.

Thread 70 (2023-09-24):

Do we need to setup yaw orientation in the PX4 vehicle setup?

FaboNo, 2023-09-24:
Dear All

I Followed the instructions and I put the px4 as shown on the pic below:
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

However when I started all the node and launched rviz, I noticed that the obstacles in the front of the drone, appeared on the left side of the drone - not in the front.

I believed that it was because I did not set up the px4 orientation - see below:

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

However once I did it, I had a lot of problem with VINS which is diverging a lot very quickly (even though I did the calibration of the extrinsics as it was described in the videos)

Someone in the community can give me some advices ?

Thank you very much for your help

Closed 2023-09-24.

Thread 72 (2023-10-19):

Does imu calibration only require calibration of white noise and random walks? Does deterministic errors such as scale, non-orthogonal coordinate system (installation error), and sensor offset need to be calibrated? If so, how can the calibration be used in the vins algorithm?

huang-shijie, 2023-10-19:

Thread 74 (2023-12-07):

out_path不飘，但是/vins_fusion/imu_propagate漂移明显

otis-XJY, 2023-12-07:
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
运行后发现vins输出的out_path不飘，但是/vins_fusion/imu_propagate中的位置漂移明显
我不知道是什么原因导致的？
我发现项目中并没有使用loop_fusion，可以请问一下具体的原因吗？
硬件：D435i+NX（fusin-gpu）

otis-XJY, 2023-12-10:
我还很好奇为什么用imu_propagate作为odom而不是vins输出的odom

mosongnan, 2023-12-28:
我也是这个问题，大佬你解决了吗？

otis-XJY, 2023-12-28:
就是定位失败出现飘逸，感觉是VINS-GPU的问题或者是哪个数据的帧率没上去，之前的环境有点乱了，没有敢刷机重做。

> 我还很好奇为什么用imu_propagate作为odom而不是vins输出的odom

这个问题猜测是因为vins输出的odom的帧率不够

otis-XJY, 2023-12-28:
> 我也是这个问题，大佬你解决了吗？

你可以分享一下你的具体环境吗，我们可以交叉比对一下

mosongnan, 2023-12-28:
> > 我也是这个问题，大佬你解决了吗？
>
> 你可以分享一下你的具体环境吗，我们可以交叉比对一下

我用的是雷迅v5的飞控jetson tx2nx和D435i，imu数据是飞控的。跑的vins-fusion

otis-XJY, 2023-12-28:
我用的是雷迅v5+的飞控，jetson nx和D435i,跑的vins-fusion-gpu。opencv4.2.0用的GPU版本。你有确定imu、图像等数据的刷新率吗

mosongnan, 2023-12-28:
> 我用的是雷迅v5+的飞控，jetson nx和D435i,跑的vins-fusion-gpu。opencv4.2.0用的GPU版本。你有确定imu、图像等数据的刷新率吗

是按教程来的，imu200hz左右，图像我也不清楚，opencv4.6.0

otis-XJY, 2023-12-28:
我最近有点忙，两周后如果您没解决希望可以和您进一步探讨

mosongnan, 2023-12-28:
> 我最近有点忙，两周后如果您没解决希望可以和您进一步探讨

好的，感谢

ffxunmeng, 2024-04-19:
> 我最近有点忙，两周后如果您没解决希望可以和您进一步探讨

想问一下大佬们，这个问题解决了吗

mosongnan, 2024-04-19:
> > 我最近有点忙，两周后如果您没解决希望可以和您进一步探讨
>
> 想问一下大佬们，这个问题解决了吗

换成nuc以后就没这个问题了，怀疑是算力问题。之前用的是jetson tx2。

Biangsama, 2024-11-09:
想问下大佬们解决了这个问题了吗，我现在也是卡在这一步了

Biangsama, 2024-11-09:
那可以用path的数据作为位置坐标呢

Biangsama, 2024-11-09:
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

那后续还有用JETSON NX解决问题吗

Biangsama, 2024-11-09:
> 我用的是雷迅v5+的飞控，jetson nx和D435i,跑的vins-fusion-gpu。opencv4.2.0用的GPU版本。你有确定imu、图像等数据的刷新率吗

大佬你后续怎么解决的呀

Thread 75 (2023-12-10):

extrinsic body_T_cam1/cam0 calibration

FaboNo, 2023-12-10:
So far I am not able to calibrate these matrices and if I take a look at `vins_fusion/imu_propagate` I can see a big divergence when I carry he drone around and come back to the start position

In order to initialize at least the translation part of the two matrices, can you tell me if the origin of the frame is centered on the PixHawk as it is shown below:
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

Thank you for your support

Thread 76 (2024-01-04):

请问如何将vins视觉定位替换为动捕定位呢

1094780291, 2024-01-04:
你好，我想在室内想尝试用动捕替换vins进行定位，但是看完代码对具体改哪块的内容还是无从下手，所以想麻烦问一下用动捕来定位怎么进行修改呢，麻烦您了

Chennnnn-a, 2024-09-05:
我把run_ctrl.launch和single_run_in_exp.launch里的/vins_fusion/imu_propagate改成了/mavros/local_position/odom，但是从手动控制切换到自主悬停的时候无人机会开始逆时针画圈，而且画圈半径越来越大，高度倒是不变。我目前没有解决上面这个问题，如果您还在替换定位方式的话可以试一下。如果您成功替换了，希望您可以分享一下怎么做的，非常感谢

jingyang-huang, 2024-10-30:
> 我把run_ctrl.launch和single_run_in_exp.launch里的/vins_fusion/imu_propagate改成了/mavros/local_position/odom，但是从手动控制切换到自主悬停的时候无人机会开始逆时针画圈，而且画圈半径越来越大，高度倒是不变。我目前没有解决上面这个问题，如果您还在替换定位方式的话可以试一下。如果您成功替换了，希望您可以分享一下怎么做的，非常感谢

有可能是你的odom消息里没有速度信息，如果没有速度的话可能就会出现画圆的情况。你检查下/twist里值是不是0

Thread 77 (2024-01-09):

通过SD卡修改IMU 200Hz无效的解决方法

MiangChen, 2024-01-09:
如果无法用里面的命令修改IMU为200Hz, 可以试一试加一句(可能是波特率之前没设置对):
mavlink start -d /dev/ttyACM0 -b 921600
mavlink stream -d /dev/ttyACM0 -s ATTITUDE_QUATERNION -r 200
mavlink stream -d /dev/ttyACM0 -s HIGHRES_IMU -r 200

cyberyang123, 2024-06-24:
还有一个办法，可以在最新版本的PX4固件上提高IMU发布频率
修改一下PX4源码，将src/modules/mavlink/mavlink_main.cpp里面有关ATTITUDE_QUATERNION、HIGHRES_IMU的参数全部修改成200.0f，应该是需要修改5处，然后编译一份固件
实测有效
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

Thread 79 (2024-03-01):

Reject AUTO_TAKEOFF

ranjithlesoko, 2024-03-01:
[ INFO] [1709288461.395479347]: PX4CTRL] Waiting for RC
[ INFO] [1709288461.402635812]: [PX4CTRL] RC received.
[ INFO] [1709288462.613087580]: [px4ctrl] Voltage=4.826, percentage=1.000
[ERROR] [1709288468.683143015]: [px4ctrl] Reject AUTO_TAKEOFF. If you have your RC connected, keep its switches at "auto hover" and "command control" states, and all sticks at the center, then takeoff again.
I'm using herelink not sort because one time its get take

striker2333, 2025-02-25:
I also encountered the same error, How did you solve this problem? Thanks!

ranjithlesoko, 2025-02-27:
@striker2333  what rc are  you using

Closed 2024-08-07.

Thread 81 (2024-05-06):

编译时出现问题

xiaoyangjun233, 2024-05-06:
make[2]: *** [realflight_modules/VINS-Fusion/camera_models/CMakeFiles/camera_models.dir/build.make:76：realflight_modules/VINS-Fusion/camera_models/CMakeFiles/camera_models.dir/src/calib/CameraCalibration.cc.o] 错误 1
make[1]: *** [CMakeFiles/Makefile2:2278：realflight_modules/VINS-Fusion/camera_models/CMakeFiles/camera_models.dir/all] 错误 2

报错如上望大佬解救

pinyinjj, 2024-05-30:
同样报错，请问怎么解决

XXLiu-HNU, 2024-06-10:
我遇到了相同的步骤，后来解决了。
解决方法是通过按照readme中的步骤，将**“realsense驱动安装”**和**“****安装ceres与glog与ddyanmic-reconfigure”**部分编译成功，之后在进行**“下载ego-planner源码并编译”**。
亲测对我自己可用，可以检查一下上边步骤是否完成

XXLiu-HNU, 2024-06-11:
先把这部分内容编译成功，再编译代码。我的就是这样解决的

XXLiu-HNU, 2024-06-11:
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
先把这部分内容编译完成，再编译后边的内容

xiaoyangjun233, 2024-12-02:
这里可以参考作者后续有在issue中提到针对不同opencv版本与c++环境如何更改。至少我的问题在更改相应函数后即可编译，如有后来的朋友们仍有问题，也希望能与我这个新手一起交流。

Closed 2024-12-02.

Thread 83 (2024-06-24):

在最新版本PX4固件中提高IMU发布频率的方法

cyberyang123, 2024-06-24:
修改一下PX4源码，将src/modules/mavlink/mavlink_main.cpp里面有关ATTITUDE_QUATERNION、HIGHRES_IMU的参数全部修改成200.0f，应该是需要修改5处，然后编译一份固件
实测有效
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

2874160799, 2024-07-27:
你这个不是才170吗？

cyberyang123, 2024-07-27:
> 你这个不是才170吗？

我这个飞控最大只能做到170，飞控算力瓶颈了

Closed 2025-06-18.

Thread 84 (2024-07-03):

无人机缓慢起飞到设定的1m时候能够稳定在那个位置，然后过一会就会突然加速冲刺，向上飞

xj1429796845, 2024-07-03:
您好，我的机架是380机型，飞控是px4  2.4.8  ，起飞的hover percent根据遥控器上油门的数值设置到0.39左右，无人机缓慢起飞到设定的1m时候能够稳定在那个位置，然后过一会就会突然加速冲刺，向上飞，每次出现这种情况我都是直接切手动降落，为什么会这样呢？

LUCKEYgirl, 2024-07-06:
我也是，有解决吗？

xj1429796845, 2024-07-07:
> 我也是，有解决吗？

暂时还没有，我先换了个飞控，下周再试飞一下，如果您解决了，能否告知一下 解决方案

LUCKEYgirl, 2024-07-07:
我解决了，是遥控器油门通道反向了！！！！您看一下是不是3通道的油门上拨，舵量变小，不然就不对，你可以仔细看一下视频，然后如果还是不行那就是  hover_percentage: 0.30  # Thrust percentage in Stabilize/Arco mode # *太大了，慢慢调小到刚刚能够起飞的感觉，最好把飞机用绳子拴住直留能够飞1m，然后飞过头就急停，机臂下面垫海绵

LUCKEYgirl, 2024-07-07:
不是飞控的问题

LUCKEYgirl, 2024-07-07:
我刚刚解决了，是遥控器油门通道反向了！！！！您看一下是不是3通道的油门上拨，舵量变小，不然就不对，你可以仔细看一下视频，然后如果还是不行那就是 hover_percentage: 0.30 # Thrust percentage in Stabilize/Arco mode # *太大了，慢慢调小到刚刚能够起飞的感觉，最好把飞机用绳子拴住直留能够飞1m，然后飞过头就急停，机臂下面垫海绵，我们之前也怀疑是飞控，目前不是飞控的问题

------------------&nbsp;原始邮件&nbsp;------------------
发件人: ***@***.***&gt;;
发送时间: 2024年7月7日(星期天) 下午3:28
收件人: ***@***.***&gt;;
抄送: ***@***.***&gt;; ***@***.***&gt;;
主题: Re: [ZJU-FAST-Lab/Fast-Drone-250] 无人机缓慢起飞到设定的1m时候能够稳定在那个位置，然后过一会就会突然加速冲刺，向上飞 (Issue #84)

我也是，有解决吗？

暂时还没有，我先换了个飞控，下周再试飞一下，如果您解决了，能否告知一下 解决方案

—
Reply to this email directly, view it on GitHub, or unsubscribe.
You are receiving this because you commented.Message ID: ***@***.***&gt;

xj1429796845, 2024-07-07:
> 我刚刚解决了，是遥控器油门通道反向了！！！！您看一下是不是3通道的油门上拨，舵量变小，不然就不对，你可以仔细看一下视频，然后如果还是不行那就是 hover_percentage: 0.30 # Thrust percentage in Stabilize/Arco mode # *太大了，慢慢调小到刚刚能够起飞的感觉，最好把飞机用绳子拴住直留能够飞1m，然后飞过头就急停，机臂下面垫海绵，我们之前也怀疑是飞控，目前不是飞控的问题
> […](#)
> ------------------&nbsp;原始邮件&nbsp;------------------ 发件人: ***@***.***&gt;; 发送时间: 2024年7月7日(星期天) 下午3:28 收件人: ***@***.***&gt;; 抄送: ***@***.***&gt;; ***@***.***&gt;; 主题: Re: [ZJU-FAST-Lab/Fast-Drone-250] 无人机缓慢起飞到设定的1m时候能够稳定在那个位置，然后过一会就会突然加速冲刺，向上飞 (Issue #84) 我也是，有解决吗？ 暂时还没有，我先换了个飞控，下周再试飞一下，如果您解决了，能否告知一下 解决方案 — Reply to this email directly, view it on GitHub, or unsubscribe. You are receiving this because you commented.Message ID: ***@***.***&gt;

我刚看了我的3通道是正确的，向上拨舵量 是变小的，那我看下是否是 hover_percentage 值太大的原因，感谢！！

LUCKEYgirl, 2024-07-07:
向上拨舵量是从下面逐渐变小的，不是上面逐渐变小的！一定注意！

LUCKEYgirl, 2024-07-07:
向上拨舵量是从下面逐渐变小的，不是上面逐渐变小的！一定注意！

------------------&nbsp;原始邮件&nbsp;------------------
发件人: ***@***.***&gt;;
发送时间: 2024年7月7日(星期天) 下午4:39
收件人: ***@***.***&gt;;
抄送: ***@***.***&gt;; ***@***.***&gt;;
主题: Re: [ZJU-FAST-Lab/Fast-Drone-250] 无人机缓慢起飞到设定的1m时候能够稳定在那个位置，然后过一会就会突然加速冲刺，向上飞 (Issue #84)

我刚刚解决了，是遥控器油门通道反向了！！！！您看一下是不是3通道的油门上拨，舵量变小，不然就不对，你可以仔细看一下视频，然后如果还是不行那就是 hover_percentage: 0.30 # Thrust percentage in Stabilize/Arco mode # 太大了，慢慢调小到刚刚能够起飞的感觉，最好把飞机用绳子拴住直留能够飞1m，然后飞过头就急停，机臂下面垫海绵，我们之前也怀疑是飞控，目前不是飞控的问题
 …
 ------------------&nbsp;原始邮件&nbsp;------------------ 发件人: @.&gt;; 发送时间: 2024年7月7日(星期天) 下午3:28 收件人: @.&gt;; 抄送: @.&gt;; @.&gt;; 主题: Re: [ZJU-FAST-Lab/Fast-Drone-250] 无人机缓慢起飞到设定的1m时候能够稳定在那个位置，然后过一会就会突然加速冲刺，向上飞 (Issue #84) 我也是，有解决吗？ 暂时还没有，我先换了个飞控，下周再试飞一下，如果您解决了，能否告知一下 解决方案 — Reply to this email directly, view it on GitHub, or unsubscribe. You are receiving this because you commented.Message ID: @.**&gt;

我刚看了我的3通道是正确的，向上拨舵量 是变小的，那我看下是否是 hover_percentage 值太大的原因，感谢！！

—
Reply to this email directly, view it on GitHub, or unsubscribe.
You are receiving this because you commented.Message ID: ***@***.***&gt;

LUCKEYgirl, 2024-07-07:
这种就是错的，需要改反相的，我们炸鸡两次了，一定要注意

------------------&nbsp;原始邮件&nbsp;------------------
发件人:                                                                                                                        "ZJU-FAST-Lab/Fast-Drone-250"                                                                                    ***@***.***&gt;;
发送时间:&nbsp;2024年7月7日(星期天) 下午4:39
***@***.***&gt;;
***@***.******@***.***&gt;;
主题:&nbsp;Re: [ZJU-FAST-Lab/Fast-Drone-250] 无人机缓慢起飞到设定的1m时候能够稳定在那个位置，然后过一会就会突然加速冲刺，向上飞 (Issue #84)

我刚刚解决了，是遥控器油门通道反向了！！！！您看一下是不是3通道的油门上拨，舵量变小，不然就不对，你可以仔细看一下视频，然后如果还是不行那就是 hover_percentage: 0.30 # Thrust percentage in Stabilize/Arco mode # 太大了，慢慢调小到刚刚能够起飞的感觉，最好把飞机用绳子拴住直留能够飞1m，然后飞过头就急停，机臂下面垫海绵，我们之前也怀疑是飞控，目前不是飞控的问题
 …
 ------------------&nbsp;原始邮件&nbsp;------------------ 发件人: @.&gt;; 发送时间: 2024年7月7日(星期天) 下午3:28 收件人: @.&gt;; 抄送: @.&gt;; @.&gt;; 主题: Re: [ZJU-FAST-Lab/Fast-Drone-250] 无人机缓慢起飞到设定的1m时候能够稳定在那个位置，然后过一会就会突然加速冲刺，向上飞 (Issue #84) 我也是，有解决吗？ 暂时还没有，我先换了个飞控，下周再试飞一下，如果您解决了，能否告知一下 解决方案 — Reply to this email directly, view it on GitHub, or unsubscribe. You are receiving this because you commented.Message ID: @.**&gt;

我刚看了我的3通道是正确的，向上拨舵量 是变小的，那我看下是否是 hover_percentage 值太大的原因，感谢！！

—
Reply to this email directly, view it on GitHub, or unsubscribe.
You are receiving this because you commented.Message ID: ***@***.***&gt;

xj1429796845, 2024-07-07:
> 这种就是错的，需要改反相的，我们炸鸡两次了，一定要注意
> […](#)
> ------------------&nbsp;原始邮件&nbsp;------------------ 发件人: "ZJU-FAST-Lab/Fast-Drone-250" ***@***.***&gt;; 发送时间:&nbsp;2024年7月7日(星期天) 下午4:39 ***@***.***&gt;; ***@***.******@***.***&gt;; 主题:&nbsp;Re: [ZJU-FAST-Lab/Fast-Drone-250] 无人机缓慢起飞到设定的1m时候能够稳定在那个位置，然后过一会就会突然加速冲刺，向上飞 (Issue #84) 我刚刚解决了，是遥控器油门通道反向了！！！！您看一下是不是3通道的油门上拨，舵量变小，不然就不对，你可以仔细看一下视频，然后如果还是不行那就是 hover_percentage: 0.30 # Thrust percentage in Stabilize/Arco mode # 太大了，慢慢调小到刚刚能够起飞的感觉，最好把飞机用绳子拴住直留能够飞1m，然后飞过头就急停，机臂下面垫海绵，我们之前也怀疑是飞控，目前不是飞控的问题 … ------------------&nbsp;原始邮件&nbsp;------------------ 发件人: @.&gt;; 发送时间: 2024年7月7日(星期天) 下午3:28 收件人: @.&gt;; 抄送: @.&gt;; @.&gt;; 主题: Re: [ZJU-FAST-Lab/Fast-Drone-250] 无人机缓慢起飞到设定的1m时候能够稳定在那个位置，然后过一会就会突然加速冲刺，向上飞 (Issue #84) 我也是，有解决吗？ 暂时还没有，我先换了个飞控，下周再试飞一下，如果您解决了，能否告知一下 解决方案 — Reply to this email directly, view it on GitHub, or unsubscribe. You are receiving this because you commented.Message ID: @.**&gt; 我刚看了我的3通道是正确的，向上拨舵量 是变小的，那我看下是否是 hover_percentage 值太大的原因，感谢！！ — Reply to this email directly, view it on GitHub, or unsubscribe. You are receiving this because you commented.Message ID: ***@***.***&gt;

我看浙大写的是，，，看echo出来的消息里哪项在缓慢变化（这项就是油门通道值），并观察它是不是由小变大
如果是由小变大，则不需要修改throttle的rc_reverse，反之改为true，，虽然我看打印rostopic echo /mavros/rc/in出来的是 由小变大，，，，，那会儿我看的是遥控器上的舵量值向上拨是由大变小，所以我直接将throttle改成true 对吧，

xj1429796845, 2024-07-07:
> 这种就是错的，需要改反相的，我们炸鸡两次了，一定要注意
> […](#)
> ------------------&nbsp;原始邮件&nbsp;------------------ 发件人: "ZJU-FAST-Lab/Fast-Drone-250" ***@***.***&gt;; 发送时间:&nbsp;2024年7月7日(星期天) 下午4:39 ***@***.***&gt;; ***@***.******@***.***&gt;; 主题:&nbsp;Re: [ZJU-FAST-Lab/Fast-Drone-250] 无人机缓慢起飞到设定的1m时候能够稳定在那个位置，然后过一会就会突然加速冲刺，向上飞 (Issue #84) 我刚刚解决了，是遥控器油门通道反向了！！！！您看一下是不是3通道的油门上拨，舵量变小，不然就不对，你可以仔细看一下视频，然后如果还是不行那就是 hover_percentage: 0.30 # Thrust percentage in Stabilize/Arco mode # 太大了，慢慢调小到刚刚能够起飞的感觉，最好把飞机用绳子拴住直留能够飞1m，然后飞过头就急停，机臂下面垫海绵，我们之前也怀疑是飞控，目前不是飞控的问题 … ------------------&nbsp;原始邮件&nbsp;------------------ 发件人: @.&gt;; 发送时间: 2024年7月7日(星期天) 下午3:28 收件人: @.&gt;; 抄送: @.&gt;; @.&gt;; 主题: Re: [ZJU-FAST-Lab/Fast-Drone-250] 无人机缓慢起飞到设定的1m时候能够稳定在那个位置，然后过一会就会突然加速冲刺，向上飞 (Issue #84) 我也是，有解决吗？ 暂时还没有，我先换了个飞控，下周再试飞一下，如果您解决了，能否告知一下 解决方案 — Reply to this email directly, view it on GitHub, or unsubscribe. You are receiving this because you commented.Message ID: @.**&gt; 我刚看了我的3通道是正确的，向上拨舵量 是变小的，那我看下是否是 hover_percentage 值太大的原因，感谢！！ — Reply to this email directly, view it on GitHub, or unsubscribe. You are receiving this because you commented.Message ID: ***@***.***&gt;

我的遥控器AT9S PRO，油门再最低的时候，我看遥控器上的舵量值居然是100。。。。。。。

xj1429796845, 2024-07-07:
> 向上拨舵量是从下面逐渐变小的，不是上面逐渐变小的！一定注意！
> […](#)
> ------------------&nbsp;原始邮件&nbsp;------------------ 发件人: ***@***.***&gt;; 发送时间: 2024年7月7日(星期天) 下午4:39 收件人: ***@***.***&gt;; 抄送: ***@***.***&gt;; ***@***.***&gt;; 主题: Re: [ZJU-FAST-Lab/Fast-Drone-250] 无人机缓慢起飞到设定的1m时候能够稳定在那个位置，然后过一会就会突然加速冲刺，向上飞 (Issue #84) 我刚刚解决了，是遥控器油门通道反向了！！！！您看一下是不是3通道的油门上拨，舵量变小，不然就不对，你可以仔细看一下视频，然后如果还是不行那就是 hover_percentage: 0.30 # Thrust percentage in Stabilize/Arco mode # 太大了，慢慢调小到刚刚能够起飞的感觉，最好把飞机用绳子拴住直留能够飞1m，然后飞过头就急停，机臂下面垫海绵，我们之前也怀疑是飞控，目前不是飞控的问题 … ------------------&nbsp;原始邮件&nbsp;------------------ 发件人: @.&gt;; 发送时间: 2024年7月7日(星期天) 下午3:28 收件人: @.&gt;; 抄送: @.&gt;; @.&gt;; 主题: Re: [ZJU-FAST-Lab/Fast-Drone-250] 无人机缓慢起飞到设定的1m时候能够稳定在那个位置，然后过一会就会突然加速冲刺，向上飞 (Issue #84) 我也是，有解决吗？ 暂时还没有，我先换了个飞控，下周再试飞一下，如果您解决了，能否告知一下 解决方案 — Reply to this email directly, view it on GitHub, or unsubscribe. You are receiving this because you commented.Message ID: @.**&gt; 我刚看了我的3通道是正确的，向上拨舵量 是变小的，那我看下是否是 hover_percentage 值太大的原因，感谢！！ — Reply to this email directly, view it on GitHub, or unsubscribe. You are receiving this because you commented.Message ID: ***@***.***&gt;

不好意思 我刚看懂了，，原先我的油门，从下往上面打的时候 ，，，那个舵量值 ，是从上面逐渐变小， 也就是你说的反了，舵量值需要从下面，，逐渐变小

LUCKEYgirl, 2024-07-07:
对的，那样是错误的

------------------&nbsp;原始邮件&nbsp;------------------
发件人: ***@***.***&gt;;
发送时间: 2024年7月7日(星期天) 晚上6:11
收件人: ***@***.***&gt;;
抄送: ***@***.***&gt;; ***@***.***&gt;;
主题: Re: [ZJU-FAST-Lab/Fast-Drone-250] 无人机缓慢起飞到设定的1m时候能够稳定在那个位置，然后过一会就会突然加速冲刺，向上飞 (Issue #84)
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
xj1429796845, 2024-07-08:
> 这种就是错的，需要改反相的，我们炸鸡两次了，一定要注意
> […](#)
> ------------------&nbsp;原始邮件&nbsp;------------------ 发件人: "ZJU-FAST-Lab/Fast-Drone-250" ***@***.***&gt;; 发送时间:&nbsp;2024年7月7日(星期天) 下午4:39 ***@***.***&gt;; ***@***.******@***.***&gt;; 主题:&nbsp;Re: [ZJU-FAST-Lab/Fast-Drone-250] 无人机缓慢起飞到设定的1m时候能够稳定在那个位置，然后过一会就会突然加速冲刺，向上飞 (Issue #84) 我刚刚解决了，是遥控器油门通道反向了！！！！您看一下是不是3通道的油门上拨，舵量变小，不然就不对，你可以仔细看一下视频，然后如果还是不行那就是 hover_percentage: 0.30 # Thrust percentage in Stabilize/Arco mode # 太大了，慢慢调小到刚刚能够起飞的感觉，最好把飞机用绳子拴住直留能够飞1m，然后飞过头就急停，机臂下面垫海绵，我们之前也怀疑是飞控，目前不是飞控的问题 … ------------------&nbsp;原始邮件&nbsp;------------------ 发件人: @.&gt;; 发送时间: 2024年7月7日(星期天) 下午3:28 收件人: @.&gt;; 抄送: @.&gt;; @.&gt;; 主题: Re: [ZJU-FAST-Lab/Fast-Drone-250] 无人机缓慢起飞到设定的1m时候能够稳定在那个位置，然后过一会就会突然加速冲刺，向上飞 (Issue #84) 我也是，有解决吗？ 暂时还没有，我先换了个飞控，下周再试飞一下，如果您解决了，能否告知一下 解决方案 — Reply to this email directly, view it on GitHub, or unsubscribe. You are receiving this because you commented.Message ID: @.**&gt; 我刚看了我的3通道是正确的，向上拨舵量 是变小的，那我看下是否是 hover_percentage 值太大的原因，感谢！！ — Reply to this email directly, view it on GitHub, or unsubscribe. You are receiving this because you commented.Message ID: ***@***.***&gt;

我已经解决了，我是直接把throttle改成了true ，然后我换了飞控，现在起飞稳稳的，感谢您，非常感谢您提供思路

LUCKEYgirl, 2024-07-08:
我们没有改throttle这个，但是您改了能够跑成功，那就也ok，我们没改，然后重新校准遥控器 ，就可以顺利起飞

xj1429796845, 2024-07-09:
> 我们没有改throttle这个，但是您改了能够跑成功，那就也ok，我们没改，然后重新校准遥控器 ，就可以顺利起飞

应该这两种方式二选一都可以，我跑了ego-planner了，再也不往天上冲了，稳稳的

XXLiu-HNU, 2025-04-04:
遇到了同样的问题，再咨询一下大佬们。

首先我的遥控器油门规则如下:

通过拨动油门位置查看mavros rc in 话题的变化

1. 当油门在**最下边**的时候输出为**999**

2. 当油门在**中间**的时候输出为**1500**，

3. 当油门在**最上边**的时候输出为**1999**；

同时我也去阅读了PX4CtrlFSM.cpp 文件，发现当无人机从自动起飞进入悬停模式之后，会根据下边这个函数计算期望位置

```
void PX4CtrlFSM::set_hov_with_rc()
{
	ros::Time now = ros::Time::now();
	double delta_t = (now - last_set_hover_pose_time).toSec();
	last_set_hover_pose_time = now;

	hover_pose(0) += rc_data.ch[1] * param.max_manual_vel * delta_t * (param.rc_reverse.pitch ? 1 : -1);
	hover_pose(1) += rc_data.ch[0] * param.max_manual_vel * delta_t * (param.rc_reverse.roll ? 1 : -1);
        // 这一行对应的应该是高度的值，根据遥控器杆量来生成期望的位置。
	hover_pose(2) += rc_data.ch[2] * param.max_manual_vel * delta_t * (param.rc_reverse.throttle ? 1 : -1);
	hover_pose(3) += rc_data.ch[3] * param.max_manual_vel * delta_t * (param.rc_reverse.yaw ? 1 : -1);

	if (hover_pose(2) < -0.3)
		hover_pose(2) = -0.3;
```

因此我有个疑问是，即使油门反向了，此时输出仍是1500，根据遥控器逻辑
```
void RC_Data_t::feed(mavros_msgs::RCInConstPtr pMsg)
{
    msg = *pMsg;
    rcv_stamp = ros::Time::now();

    for (int i = 0; i < 4; i++)
    {
        // 当油门在中位的时候，ch[2]应该是0
        ch[i] = ((double)msg.channels[i] - 1500.0) / 500.0;
        if (ch[i] > DEAD_ZONE)
            ch[i] = (ch[i] - DEAD_ZONE) / (1 - DEAD_ZONE);
        else if (ch[i] < -DEAD_ZONE)
            ch[i] = (ch[i] + DEAD_ZONE) / (1 - DEAD_ZONE);
        else
            ch[i] = 0.0;
    }
```
此时ch[2]应该已知是0，为什么无人机会不断往天上飞。因此不太理解为什么会出现这个问题。

chenfch3, 2025-05-02:
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

> 	hover_pose(2) += rc_data.ch[2] * param.max_manual_vel * delta_t * (param.rc_reverse.throttle ? 1 : -1);
You shoule set param.rc_reverse.throttle to true and the  (param.rc_reverse.throttle ? 1 : -1) will set to 1.

Closed 2024-11-11.

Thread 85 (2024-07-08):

自动起飞失败？

x710777335, 2024-07-08:
按照步骤里面操作，运行roslaunch px4ctrl run_ctrl.launch，然后再运行sh shfiles/takeoff.sh发现电机没有转动，提示reject auto_takeoff no odom ego_planner。我是用激光雷达fast-lio作为定位源的，需要改什么吗？

zhao6868999, 2024-12-09:
Hello, I have also encountered this problem. How did you solve it？

Closed 2024-07-08.

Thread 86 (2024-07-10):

请问Fast-Drone-250的位置控制和速度控制是否简化了？

lminjy, 2024-07-10:
我的基于ego-planner的探索算法给出的是PositionCommand.msg，它设定了目标点的期望位置、速度、加速度，我的仿真环境需要的控制指令是mavros_msgs/AttitudeTarget，按照px4飞控的多旋翼的控制架构来说，仿真环境里的飞控应该是有相应的角度、角速度控制器，所以为了控制仿真环境里的四旋翼，我需要实现对应的Position Controller、Velocity Controller和Acceleration and Yaw to Attitude，并在必要的地方加入前馈控制以使四旋翼在目标点处有期望的速度、加速度，可是我在Fast-Drone-250的px4ctrl只找到Acceleration and Yaw to Attitude（是在PX4CtrlFSM.cpp中controller.calculateControl计算吧？），请问是否存在对应的Position Controller和Velocity Controller？我该如何找到它们呢？
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

lminjy, 2024-07-10:
好像是有Position Controller和Velocity Controller，但是和我理解的不太一样，按照我的理解(如方框图所示)：
位置控制器的控制输出量 $des\\_p=k_p*(des.p-odom.p)$
速度控制器期望值(控制输入量) $des\\_p+des.v-odom.v$
速度控制器的控制输出量 $des\\_v=k_v*(des\\_p+des.v-odom.v)$
因此 $des\\_acc=des.a + k_v*(des\\_p+des.v-odom.v)=des.a + k_v*(des.v-odom.v)+k_v\*k_p*(des.p-odom.p)$
所以，您是把kv*kp合成一个参数是吗？此"kv"非常规的kv是吗？

lminjy, 2024-07-11:
还有个疑问，这样算前馈控制吗？des_p的单位是m，des.v和odom.v的单位是m/s，这样直接加可以吗？

XXLiu-HNU, 2024-10-28:
【无人机系统 - 高飞组超全讲解！2021ROS暑期学校 第五天精剪回放】 https://www.bilibili.com/video/BV1Jq4y1T7QD/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

XXLiu-HNU, 2024-10-28:
> 【无人机系统 - 高飞组超全讲解！2021ROS暑期学校 第五天精剪回放】 https://www.bilibili.com/video/BV1Jq4y1T7QD/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

这里边有无人机控制部分的内容

Closed 2024-11-05.

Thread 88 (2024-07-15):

d435i position位置很飘

2874160799, 2024-07-15:
查看vins_fusion/imu_propagate话题，没动相机，但是相机的position一直在飘，是什么原因呢
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
也经常出现wait for imu的信息
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

XXLiu-HNU, 2024-10-29:
Q: VINS飘怎么办？
A: 1. 检查环境中是否有强反光物体（瓷砖、玻璃等）
   2. 尽量缓慢地移动无人机，场景内不要有运动物体
   3. 尽量准确地测量初始外参
   4. 不要在运行vins的时候在远程桌面上运行rviz（会占用大量CPU资源），实在想开建议去配一下ROS多机，然后在笔记本上开
   5. 检查环境中是否有频闪光源（肉眼无法看出，在realsense的单目画面中检查）

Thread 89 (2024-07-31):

遥控控制和命令控制问题

program123456, 2024-07-31:
为什么在启动自动起飞脚本后，无人机可以起飞，但是遥控器无法对其控制，且没有进入定点模式（无人机会飘走，可以确定视觉里程计正常启动），且在rviz内给点时，有规划出一条路径但是无人机没有响应。
感觉像是nuc给的指令飞控没有执行

XXLiu-HNU, 2024-10-29:
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
阅读状态机代码，理论上自动起飞达到高度之后就会进入hover模式

观察状态机终端中打印的状态，另外确定遥控器六通正常

program123456, 2024-11-02:
好的，谢谢

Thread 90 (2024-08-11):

想问一下为什么要在设置中关闭SYS_USE_IO

lianghanfang, 2024-08-11:
想在飞机上装个舵机，但是这一个把IO PWM给关了，想请问一下为什么要关闭呢

XXLiu-HNU, 2025-04-04:
在csdn里看到的：

**_开启FMU输出
首先设置SYS_USE_IO=0。对于Pixhawk 4而言，为了扩展IO口，单独引入了IO处理器，通常咱们的PWM电调就是接在这上面的，但是对于DShot的电调而言，我们为了追求更小的延迟，如果我们还接在IO处理上，这样就会造成不必要的延迟，因为我们的计算都是在FMU上进行计算的，如果FMU把控制量发送到IO板子再到电调的话就会有大概5.4ms左右的延迟，所以我们需要把电机输出绑定在FMU上，修改SYS_USE_IO参数就是完成这一步骤的。_**

https://blog.csdn.net/qq_38649880/article/details/121522724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

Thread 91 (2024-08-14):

Not able to fly real system with the planner

ta-jetson, 2024-08-14:
Hey, (@ZJU-jxlin, @bigsuperZZZX )

Firstly - Congrats on this amazing planner and thanks for this contribution.

I am trying to replicate this setup using a jetson orin nano, FC with PX4 1.14, D435i and T265. I get the odometry from T265 and depth (& pointcloud) from D435.

This is my launch file

```
<launch>
    <!-- number of moving objects -->
    <arg name="obj_num" value="1" />
    <arg name="drone_id" value="0"/>

    <arg name="map_size_x" value="100"/>
    <arg name="map_size_y" value="50"/>
    <arg name="map_size_z" value="3.0"/>
    <arg name="odom_topic" value="/camera/odom/sample"/>

    <!-- main algorithm params -->
    <include file="$(find ego_planner)/launch/advanced_param_exp.xml">
        <arg name="drone_id" value="$(arg drone_id)"/>
        <arg name="map_size_x_" value="$(arg map_size_x)"/>
        <arg name="map_size_y_" value="$(arg map_size_y)"/>
        <arg name="map_size_z_" value="$(arg map_size_z)"/>
        <arg name="odometry_topic" value="$(arg odom_topic)"/>
        <arg name="obj_num_set" value="$(arg obj_num)" />

        <!-- camera pose: transform of camera frame in the world frame -->
        <!-- depth topic: depth image, 640x480 by default -->
        <!-- don't set cloud_topic if you already set these ones! -->
        <arg name="camera_pose_topic" value="/pcl_render_node/camera_pose"/>
        <arg name="depth_topic" value="/pcl_render_node/depth"/>

        <!-- topic of point cloud measurement, such as from LIDAR  -->
        <!-- don't set camera pose and depth, if you already set this one! -->
        <arg name="cloud_topic" value="/camera_d435/depth/color/points"/>

        <!-- intrinsic params of the depth camera -->
        <arg name="cx" value="321.735473632812"/>
        <arg name="cy" value="243.194213867188"/>
        <arg name="fx" value="384.127471923828"/>
        <arg name="fy" value="384.127471923828"/>

        <!-- maximum velocity and acceleration the drone will reach -->
        <arg name="max_vel" value="1.0" />
        <arg name="max_acc" value="4.0" />
        <!--always set to 1.5 times grater than sensing horizen-->
        <arg name="planning_horizon" value="6" />
        <arg name="use_distinctive_trajs" value="false" />
        <!-- 1: use 2D Nav Goal to select goal  -->
        <!-- 2: use global waypoints below  -->
        <arg name="flight_type" value="1" />
        <!-- global waypoints -->
        <!-- It generates a piecewise min-snap traj passing all waypoints -->
        <arg name="point_num" value="1" />
        <arg name="point0_x" value="15" />
        <arg name="point0_y" value="0" />
        <arg name="point0_z" value="1" />
        <arg name="point1_x" value="0.0" />
        <arg name="point1_y" value="0.0" />
        <arg name="point1_z" value="1.0" />
        <arg name="point2_x" value="15.0" />
        <arg name="point2_y" value="0.0" />
        <arg name="point2_z" value="1.0" />
        <arg name="point3_x" value="0.0" />
        <arg name="point3_y" value="0.0" />
        <arg name="point3_z" value="1.0" />
        <arg name="point4_x" value="15.0" />
        <arg name="point4_y" value="0.0" />
        <arg name="point4_z" value="1.0" />
    </include>
    <!-- trajectory server -->
    <node pkg="ego_planner" name="drone_$(arg drone_id)_traj_server" type="traj_server" output="screen">
        <!-- <remap from="position_cmd" to="/setpoints_cmd"/> -->
        <remap from="/position_cmd" to="planning/pos_cmd"/>
        <remap from="~planning/bspline" to="drone_$(arg drone_id)_planning/bspline"/>
        <param name="traj_server/time_forward" value="1.0" type="double"/>
    </node>

    <!-- Static Transform between camera_link and camera_d435_link -->
    <<node pkg="tf2_ros" type="static_transform_publisher" name="t265_to_d435" args="0 0 0 0 0 0 camera_odom_frame camera_d435_link" />

</launch>

```

There are issues. I don't know if these issues are interrelated.

1. There is no frame called world. Absence of a world frame prevents me from doing any transforms and displaying the pointcloud.

2. When the planner starts, the body's visualization moves much faster than the actual system. It also follows weird trajectories and keep going in to random point in random directions before reaching the target node. (No obstacles, open environment)

3.I read that the actual experiments were carried out with d435i only, (Odometry was estimated using VINS (Using the IR cameras)). I am using two differnt cameras for pose and depth. Do I need to add some code to get it working or is changing the topic and static transforms enough?

[have tried enabling CUDA and using depth instead of cloud, makes no difference]
When giving depth, I don't have a topic that publishes pose (camera) ; so i decided to give cloud.
I am actively testing this system. Any suggestions would be helpful.

(P.S : I know this repo is out of maintainence, but the same issue occurs in ego-planner-swarm)

Thank you

ta-jetson, 2024-08-20:
> Excuse me, how do you give the number of seats to make the plane fly at once? After I modified the flight mode according to the code explanation part in the video, I still could not achieve this task.

I don't know what you mean by seats. As for flight mode, when I give a point, I switch to offboard mode. (PX4 1.14)

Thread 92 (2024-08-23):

I can only change IMU frequency , It also show Odom frequency is too low.

hcws, 2024-08-23:
```
mavlink stream -d /dev/ttyACM0 -s ATTITUDE_QUATERNION -r 200
mavlink stream -d /dev/ttyACM0 -s HIGHRES_IMU -r 200
```
I use cmds above to increase IMU and Odom frequency ， but the I can only change IMU frequency , It also show Odom frequency is too low.

ta-jetson, 2024-08-27:
The commands you running only increase the frequency of imu and not the frequency of odometry.

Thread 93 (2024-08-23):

why not use /mavros/setpoint_velocity/cmd_vel control？

hcws, 2024-08-23:
why not use `/mavros/setpoint_velocity/cmd_vel` control？

XXLiu-HNU, 2024-10-29:
为了更好的控制效果，[【无人机系统 - 高飞组超全讲解！2021ROS暑期学校 第五天精剪回放】 https://www.bilibili.com/video/BV1Jq4y1T7QD/?share_source=copy_web&vd_source=694800f4f1ae99186a15066decbc1bc2](url)
参考第3部分，无人机控制

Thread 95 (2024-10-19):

Drone Oscillation During Takeoff with LiDAR Using px4ctrl

bhaskar-glitch, 2024-10-19:
I am currently using **px4ctrl** (https://github.com/ZJU-FAST-Lab/Fast-Drone-250/tree/master/src/realflight_modules/px4ctrl) with the **Fast LIO** algorithm (https://github.com/hku-mars/FAST_LIO), running on Pixhawk Cube+ with PX4 firmware version 1.15.0 and a Livox Mid360 LiDAR for odometry.

When executing an automatic takeoff via the takeoff.sh script, the drone lifts off but starts oscillating along both the X and Z axes. Previously, I used a camera for odometry with px4ctrl, and it worked flawlessly. However, after switching to LiDAR, this oscillation issue has appeared.

I am attaching the flight log for reference. Kindly review and provide assistance. Thank you!

Flight Log:- https://drive.google.com/file/d/18RDbIVaIRgQszmVV3RXJ6CHgbowOQn8K/view?usp=drive_link

PanNeng-ZJU, 2024-11-11:
From the log, I see that your drone's accleration estimation is going throught big oscillation of +- 8m/s^2, you should firstly fix the oscillation or the odometry is too bad for the drone to conduct feedback control. The problem might lies in your drone's frame that lacks stiffness.

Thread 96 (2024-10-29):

自动起飞时无人机向左飘/无人机实际位置和规划出来的轨迹存在误差

XXLiu-HNU, 2024-10-29:
### **背景：**
采用的机架为450机架，飞控为Cuav X7+ ，动力套件正常，在RTK模式下定点模式稳定
修改 `ctrl_param_fpv.yaml` 文件中的 `mass`，PID参数 `Kp0 …`从1.5修改为2

### **问题1：**
执行自动起飞的时候，无人机会向左方平移大概**20cm**的距离，然后上升到1m的距离。应该不是什么大问题，但是出现了问题2，怀疑和问题1类似，附上视频，具体体现在视频的1s-3s区间：
https://github.com/user-attachments/assets/afea5c59-82da-4c89-a78e-7710202974bb

### **问题2：**
不确定是否和 **问题一** 存在关联，通过录包会看的过程，发现无人机的轨迹（绿色细线段）和规划出来的轨迹（红色粗线段）存在一定的偏差，同样是往左偏移大概 **20cm** 的距离， **实际飞行中发现VINS定位未发生漂移情况**

### 推断可能的原因：

1. 无人机传感器需要校准，因为实验过程中发生了几次摔机，可能传感器需要校准
2. 控制部分参数需要修改，因为使用的飞机和教程中的飞机存在区别

### 希望实现的效果
无人机准确的跟踪生成的轨迹，从而实现正确的避障行为

XXLiu-HNU, 2024-10-29:
通过重新校准飞机的传感器，实现了精准的跟踪

unius589, 2025-01-21:
您好,最近也在复现这个项目.我的飞机也是大轴距, 我现在飞机起飞后会有左右漂移的问题.  现在想调整一下pid参数, 具体思路有点混乱, 想跟你请教一下:
1. 我看它这个项目只能调整ctrl_param_fpv.yam文件中的pid参数, 我的理解是这个跟踪控制是在程序中controller.cpp实现的, 底层飞控px4的唯一作用就是执行上层的控制指令(话题为/mavros/setpoint_raw/attitude), 而跟和px4自身的pid参数是无关, 不知这样理解对不对?
2.  您提到的无人机轨迹 和 规划出来的轨迹的对比, 具体是指什么? 是无人机的里程计/odom  和  des.p的信息吗?

谢谢

unius589, 2025-01-21:
@XXLiu-HNU 您好,最近也在复现这个项目.我的飞机也是大轴距, 我现在飞机起飞后会有左右漂移的问题. 现在想调整一下pid参数, 具体思路有点混乱, 想跟你请教一下:

    我看它这个项目只能调整ctrl_param_fpv.yam文件中的pid参数, 我的理解是这个跟踪控制是在程序中controller.cpp实现的, 底层飞控px4的唯一作用就是执行上层的控制指令(话题为/mavros/setpoint_raw/attitude), 而跟和px4自身的pid参数是无关, 不知这样理解对不对?
    您提到的无人机轨迹 和 规划出来的轨迹的对比, 具体是指什么? 是无人机的里程计/odom 和 des.p的信息吗?

谢谢

unius589, 2025-01-21:
您好,最近也在复现这个项目.我的飞机也是大轴距, 我现在飞机起飞后会有左右漂移的问题. 现在想调整一下pid参数, 具体思路有点混乱, 想跟你请教一下:

1. 我看它这个项目只能调整ctrl_param_fpv.yam文件中的pid参数, 我的理解是这个跟踪控制是在程序中controller.cpp实现的, 底层飞控px4的唯一作用就是执行上层的控制指令(话题为/mavros/setpoint_raw/attitude), 而跟和px4自身的pid参数是无关, 不知这样理解对不对?
2. 您提到的无人机轨迹 和 规划出来的轨迹的对比, 具体是指什么? 是无人机的里程计/odom 和 des.p的信息吗?

谢谢

unius589, 2025-01-21:
@XXLiu-HNU

XXLiu-HNU, 2025-01-21:
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
首先我也不是专门做控制的，这是我自己的一些看法：
1. 这里的PID是根据期望位置和当前位置的偏差，计算控制量，具体你可以参考[control.cpp](https://github.com/ZJU-FAST-Lab/Fast-Drone-250/blob/master/src/realflight_modules/px4ctrl/src/controller.cpp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)。这个PID参数和飞控类似，不过他给的默认的参数基本上都是可以用的，左右飘一般不是PID参数的问题，我猜测是飞控IMU未增加减震模块或者飞控传感器未校准。 这里的PID并不是和自身PID无关，因为一般飞控可以直接输入位置控制（setpoint/local_pose）这个时候飞控自己就需要进行位置环和姿态环的PID参数控制，相当于这里单独把位置环拿出来，自己计算，然后位置环还是飞控进行控制。
2. 这里是指：规划的轨迹（规划的轨迹） 与 无人机的实际位置（odom），表现在RVIZ中无人机的轨迹（绿色）和规划的路径（红色）不重合
3. 建议你校准一下传感器，然后看看IMU是不是震动太大

XXLiu-HNU, 2025-01-21:
> [@XXLiu-HNU](https://github.com/XXLiu-HNU)

这里有关于控制部分理论的讲解：【无人机系统 - 高飞组超全讲解！2021ROS暑期学校 第五天精剪回放】 https://www.bilibili.com/video/BV1Jq4y1T7QD/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

unius589, 2025-02-08:
@XXLiu-HNU 感谢回答！突然有个疑问，按照这个逻辑，其实位置和速度控制也放到PX4底层去做，也就是我们只给飞控发送位置控制指令；这样是否会 位置和速度控制放在上层去做要更好？

unius589, 2025-02-08:
还有，飞控需要执行姿态环（及角速度环）的控制，那么姿态环的PID参数理论上也需要在QGC中进行设置调整的对吧？

XXLiu-HNU, 2025-02-08:
> @XXLiu-HNU 感谢回答！突然有个疑问，按照这个逻辑，其实位置和速度控制也放到PX4底层去做，也就是我们只给飞控发送位置控制指令；这样是否会 位置和速度控制放在上层去做要更好？

这个需要看你的需求，如果无人机的轨迹没有很激进，只用位置控制也是可以的（个人意见），高飞老师在 b 站说想复现他们的项目最好参考他们的控制器逻辑

XXLiu-HNU, 2025-02-08:
> 还有，飞控需要执行姿态环（及角速度环）的控制，那么姿态环的PID参数理论上也需要在QGC中进行设置调整的对吧？

是的，这个项目给的参数是一些比较通用的参数，针对自己的飞机可以自己调整来适配已实现更好的效果

Closed 2024-10-29.

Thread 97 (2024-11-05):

How to increase hz of IMU and odom

NamDinhRobotics, 2024-11-05:
Thanks for your great work,
I am struggling to increase the IMU and odometry (odom) frequency of PX4, following your guide:

"Create a file named /etc/extras.txt in the root directory of the flight controller's SD card. Write the following lines into the file:
```
mavlink stream -d /dev/ttyACM0 -s ATTITUDE_QUATERNION -r 200
mavlink stream -d /dev/ttyACM0 -s HIGHRES_IMU -r 200
```
This will increase the frequency of the IMU."

I inserted an SD card, created the /etc/extras.txt file, and copied the following lines into it:
```
mavlink stream -d /dev/ttyACM0 -s ATTITUDE_QUATERNION -r 200
mavlink stream -d /dev/ttyACM0 -s HIGHRES_IMU -r 200
```

However, the MAVROS topics for IMU and odometry are still only reporting at 50 Hz.
Could you please help me with this? ( any note dor this)

bests,

Closed 2024-11-19.

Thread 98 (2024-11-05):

IMU problem and automatic takeoff error

yanjifa666, 2024-11-05:
I am using a 6c flight controller. I increased the frequency of the imu through commands. However, when testing automatic takeoff, it still prompts that the frequency is too low and the odometer speed is too high, so the takeoff is restricted.
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

PanNeng-ZJU, 2024-11-11:
You should firstly check the IMU frequency by the command "rostopic hz /mavros/imu/data" to see if you have really increased the frequency. As for the high odometry speed, it's obviously that the odometry has broken down, and you should check it first.

yanjifa666, 2024-11-25:
Thank you, it has been solved. But before each takeoff, I have to use the command line to increase the imu frequency. (I use a 6c flight controller)

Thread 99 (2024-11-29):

Is the controller conservative/simplified?

XXLiu-HNU, 2024-11-29:
### Question 1 (・∀・*)
Is the open source linear controller in the project a bit simplified? Through simulation and physical tests, it is found that when the drone speed is high (1m/s or above), collisions will occur, and the reproduction effect is not as aggressive and robust as shown in the video. **I would like to ask what the controller used by your group during the experiment looks like?**

### Question 2 (・∀・*)
In addition, **what is the difference between [so3_control](https://github.com/ZJU-FAST-Lab/Fast-Drone-250/tree/master/src/uav_simulator/so3_control) in the simulation and [px4ctrl](https://github.com/ZJU-FAST-Lab/Fast-Drone-250/tree/master/src/realflight_modules/px4ctrl) in the real thing?** If the former is transplanted to the physical experiment, will the control effect be better?

Thank you for open-sourcing such an excellent project, looking forward to your reply(●'◡'●)

XXLiu-HNU, 2025-01-11:
px4ctrl中的控制器线性控制器，可以时间低速的飞行。如果想修改的话可以使用MPC或者LQR，或者更加复杂的PID

Closed 2025-01-11.

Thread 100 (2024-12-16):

Automatic takeoff failed, but there were no errors reported

zhao6868999, 2024-12-16:
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
The first takeoff prompt showed a low IMU frequency. After using the mavlink command to increase the frequency, running the takeoff command again resulted in no error messages. Is there anyone who can answer this question?

XXLiu-HNU, 2024-12-18:
1. Check the UAV state in QGC or mavros/state, is armed and offboarded?
2. Make sure the RC's set is right
3. In [PX4CtrlFSM.cpp](https://github.com/ZJU-FAST-Lab/Fast-Drone-250/blob/master/src/realflight_modules/px4ctrl/src/PX4CtrlFSM.cpp) , you can add ROSINFO for get the FSM's state
4. Something else possible...

zhao6868999, 2024-12-20:
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

Hello, can you explain the third point in detail?

XXLiu-HNU, 2024-12-20:
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

在px4ctrl中，控制器状态机是从munual control 到 auto takeoff 其中触发条件是遥控器设置正确且档位正确，接收到起飞的话题。因为你可以看一下状态机处于什么状态，如果处于手动控制，说明是因为没有成功进入自动起飞模式，如果是在自动起飞，而没有起飞 可能是因为“自动起飞”中有bug，先试着缩小问题的范围

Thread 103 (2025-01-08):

构建简化版的px4ctrl

Jamin-Yang, 2025-01-08:
我想在px4ctrl的基础上进行修改，只使用x-y平面的速度和yaw角的旋转速率进行飞行控制。我可以直接去掉des.a和des.p吗？
 des_acc(0) = Kv(0) * (des.v(0) - odom.v(0));
  des_acc(1) = Kv(1) * (des.v(1) - odom.v(1));
  des_acc(2) = 0.0;
  des_acc += Eigen::Vector3d(0, 0, param_.gra);

XXLiu-HNU, 2025-01-11:
这px4ctrl最后用到的话题输出是
```
fsm.ctrl_FCU_pub = nh.advertise<mavros_msgs::AttitudeTarget>("/mavros/setpoint_raw/attitude", 10);
```

简化为速度输出可以使用`/mavros/setpoint_velocity`话题

SriKrishnaKalyan5, 2025-05-15:
你好，有人可以建议我在哪里发布这个 cmd 主题吗？
https://github.com/ZJU-FAST-Lab/Fast-Drone-250/blob/8ff64274b161bb829653faf5946656658e7e2c9f/src/realflight_modules/px4ctrl/src/px4ctrl_node.cpp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

XXLiu-HNU, 2025-05-15:
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

https://github.com/ZJU-FAST-Lab/Fast-Drone-250/blob/8ff64274b161bb829653faf5946656658e7e2c9f/src/planner/plan_manage/src/traj_server.cpp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

XXLiu-HNU, 2025-05-15:
> [@XXLiu-HNU](https://github.com/XXLiu-HNU) Yes I see that, but the topic names are different, and from what I understand they should be the same in order to communicate, right?

In the launch file, it uses remap to correspond to the topic name:
https://github.com/ZJU-FAST-Lab/Fast-Drone-250/blob/8ff64274b161bb829653faf5946656658e7e2c9f/src/realflight_modules/px4ctrl/launch/run_ctrl.launch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

SriKrishnaKalyan5, 2025-05-15:
@XXLiu-HNU  Ohhhh Perfect.... Thank you so much for that i missed to go through launch files.... This helps a lot...

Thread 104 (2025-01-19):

自动起飞失败

unius589, 2025-01-19:
你好，咨询一下自动起飞失败的问题；我换了机架，轴距是400，自动起飞前VINS都没问题，里程计信息也正常；自动起飞脚本运行后电机加速旋转，但就是飞不起来，具体见视频；
因为考虑到安全问题，飞机外面增加了一个塑料的罩子，整机重量2.9kg，轴距400，7寸三叶桨；

目前做过以下尝试：
0. 已尝试增加hover_percentage的值，从0.3一路增加到0.6都飞不起来。
1. 已确认螺旋桨没有装反；
2. 电机用的KV值的 1100，力效表见图片。按照表格推算，0.55油门时，单个电机推力达到1kg多，总推力足以超过飞机重量啊；

<!-- Failed to upload "petal_20250119_111005.mp4" -->

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

111005.mp4" -->

可能原因是什么呢？麻烦帮忙分析下，谢谢

unius589, 2025-01-19:
视频上传失败了，看这个链接吧  https://www.bilibili.com/video/BV1uuwqeJEgn/?spm_id_from=333.999.0.0

PanNeng-ZJU, 2025-02-24:
悬停油门继续调高试试？

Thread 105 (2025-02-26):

ARM rejected by PX4!

joexsyd, 2025-02-26:
请问使用px4ctrl这套状态机，上电后  有时候就能正常解锁起飞，硬件软件都没有动  ，然后有时候 就显示无法解锁 ARM rejected by PX4!，
是在下面的函数中，  mavros state显示正常连接 。  需要重新启动飞控，有时候得重启电脑再运行程序才能正常解锁，请问您有遇到过类似的问题吗  ，总是不定期的无法解锁

		if (param.takeoff_land.enable_auto_arm)
			{
				toggle_arm_disarm(true);
			}

blowfish9423, 2025-03-16:
我也遇到同样的问题，重新校准，重启，一直没有解决

anyi12433, 2025-05-11:
我们也遇到同样的问题，尝试给脚本chmod加权限，报错消失，但是飞机没有反应，有人解决了吗

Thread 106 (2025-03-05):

rviz中重建点云异常

A-close-observer, 2025-03-05:
您好！
我们在运行vins时，出现这样的报错
ERROR] [1559609392.397215054]: Ignoring transform for child_frame_id "camera_color_frame" from authority "unknown_publisher" because of an invalid quaternion in the transform (0.000000 -0.500000 0.000000 0.000000)

[ERROR] [1559609392.397275743]: Ignoring transform for child_frame_id "camera_color_frame" from authority "unknown_publisher" because of an invalid quaternion in the transform (0.000000 -0.500000 0.000000 0.000000)

A-close-observer, 2025-03-24:
注意设置膨胀系数，特别是在狭窄场地测试时，很容易误认为重建出现问题

Closed 2025-03-09.

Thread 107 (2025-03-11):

PID Controller的疑惑

ZhangZhangZhangzzz, 2025-03-11:
在PID Controller中，对于这些参数的具体含义有一些疑惑。

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
第一个疑惑是kp与kv的含义
我对于Kp0，Kp1,Kp2（Kv0,kv1,kv2）的理解如下：
kp0，kp1，kp2分别代表x，y，z轴的位置环(而kv代表速度环)
不知道理解的是否正确。

第二个疑惑是x，y，z轴相对于机身是处在什么样的位置，例如z表示垂直与地面的轴，而x轴，y轴，哪个轴代表着飞机正向的方向？？

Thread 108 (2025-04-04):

可不可以使用MID360 的IMU作为px4ctrl的输入

XXLiu-HNU, 2025-04-04:
目前遇到无人机在自动起飞的时候总是左右晃动，怀疑是飞控自身IMU的减震比较差（NxtPx4 v2）

因此想直接使用MID360雷达的IMU，不知道可不可以

XXLiu-HNU, 2025-04-07:
https://github.com/ZJU-FAST-Lab/ego-planner/issues/112#issuecomment-2581663730

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

后续会进行测试，看看效果如何

chenfch3, 2025-04-27:
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

hello, have you tested it? I found a comment [nh.subscribe<sensor_msgs::Imu>("/mavros/imu/data", // Note: do NOT change it to /mavros/imu/data_raw !!!](https://github.com/ZJU-FAST-Lab/Fast-Drone-250/blob/8ff64274b161bb829653faf5946656658e7e2c9f/src/realflight_modules/px4ctrl/src/px4ctrl_node.cpp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). The imu created by livox was raw. How did you fixed it at the end?

XXLiu-HNU, 2025-04-27:
> hello, have you tested it? I found a comment [nh.subscribe<sensor_msgs::Imu>("/mavros/imu/data", // Note: do NOT change it to /mavros/imu/data_raw !!!](https://github.com/ZJU-FAST-Lab/Fast-Drone-250/blob/8ff64274b161bb829653faf5946656658e7e2c9f/src/realflight_modules/px4ctrl/src/px4ctrl_node.cpp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). The imu created by livox was raw. How did you fixed it at the end?

实际上我们两种都测试了，效果差不多，不需要额外处理raw的问题。

但是有一个机架雷达的imu震动较大，[hku_mars 作者建议使用飞控的imu作为输入](https://github.com/hku-mars/SUPER-Hardware/issues/6#issuecomment-2823466325)

XXLiu-HNU, 2025-05-15:
更新一下，后边我们还是没用px4ctrl，因为没有找到具体的BUG，飞机也摔坏了好几次！不过借鉴px4ctrl自己写了一个[控制器](https://github.com/HNU-CAT/pid_ctrl)，现在飞的稳稳的！

[测试效果](https://github.com/user-attachments/assets/28321dd7-60d3-4f61-940d-227ff98c5790)

SriKrishnaKalyan5, 2025-05-15:
你好，有人可以建议我在哪里发布这个 cmd 主题吗？
https://github.com/ZJU-FAST-Lab/Fast-Drone-250/blob/8ff64274b161bb829653faf5946656658e7e2c9f/src/realflight_modules/px4ctrl/src/px4ctrl_node.cpp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

SuperLDG, 2025-07-26:
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

大佬您好，想请教您一下，使用mid360实现，目前用的fastlio的odom，也修改了single _run_exp.launch的里程计话题和点云话题，px4ctrl中的里程计话题也修改了，完成这样就能实现用雷达定位完成egoplanner 的避障效果了吗，目前手持雷达运动，egoplanner的规划是会随着变化的，就是没有上无人机，不知道目前的工作可行吗

SuperLDG, 2025-07-26:
以及，您有做过tf转换的工作吗，还是直接使用fastlio输出的odomtry就行了

XXLiu-HNU, 2025-07-26:
> 以及，您有做过tf转换的工作吗，还是直接使用fastlio输出的odomtry就行了

lio可以通过imu差值来实现更高的输出频率，参考vins，一般是提高到imu的频率（200hz），没有做TF变换

quinnym233, 2025-08-25:
[ERROR] [1756119541.847344188]: Ran out of pool, index=92 100 18
[ERROR] [1756119541.847388574]: Unable to handle the initial or end point, force return!
[ERROR] [1756119541.847409566]: a star error, force return!
[ERROR] [1756119541.847451808]: ERROR! the drone is in obstacle. This should not happen.
[ERROR] [1756119541.847474720]: Ran out of pool, index=95 100 15
[ERROR] [1756119541.847491105]: Unable to handle the initial or end point, force return!
[ERROR] [1756119541.847507489]: a star error
iter=5,time(ms)=0.099,rebound.
[ERROR] [1756119541.847558243]: ERROR! the drone is in obstacle. This should not happen.
[ERROR] [1756119541.847579332]: Ran out of pool, index=83 100 27
[ERROR] [1756119541.847596164]: Unable to handle the initial or end point, force return!
[ERROR] [1756119541.847608836]: a star error
iter=5,time(ms)=0.081,rebound.
[ERROR] [1756119541.847642374]: ERROR! the drone is in obstacle. This should not happen.
[ERROR] [1756119541.847660902]: Ran out of pool, index=99 100 12
[ERROR] [1756119541.847675271]: Unable to handle the initial or end point, force return!
[ERROR] [1756119541.847687879]: a star error
iter=5,time(ms)=0.072,rebound.
[ERROR] [1756119541.847720136]: ERROR! the drone is in obstacle. This should not happen.
[ERROR] [1756119541.847738857]: Ran out of pool, index=100 100 12
[ERROR] [1756119541.847751561]: Unable to handle the initial or end point, force return!
[ERROR] [1756119541.847764809]: a star error
iter=5,time(ms)=0.072,rebound.
[ERROR] [1756119541.847798090]: ERROR! the drone is in obstacle. This should not happen.
[ERROR] [1756119541.847845452]: Ran out of pool, index=100 98 11
[ERROR] [1756119541.847874989]: Unable to handle the initial or end point, force return!
[ERROR] [1756119541.847891085]: a star error

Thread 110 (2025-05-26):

README内容修改建议：libcxsparse3.1.2 改为 libcxsparse3

Heart-of-engine, 2025-05-26:
在安装ceres、glog与ddyanmic-reconfigure时，输入`sudo apt-get install liblapack-dev libsuitesparse-dev libcxsparse3.1.2 libgflags-dev libgoogle-glog-dev libgtest-dev`后，
出现报错`E: 无法定位软件包 libcxsparse3.1.2`
经过查询，发现在Ubuntu20.04版本中，libcxsparse这个包的版本已经全部改成3了，建议将上述内容改为
`sudo apt-get install liblapack-dev libsuitesparse-dev libcxsparse3 libgflags-dev libgoogle-glog-dev libgtest-dev`

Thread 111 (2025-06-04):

使用flight_type=2模式飞行waypoints不能进入状态机

wjw112211, 2025-06-04:
您好，我们使用下面这种模式飞行的时候：

```
<arg name="flight_type" value="2" />

<arg name="point_num" value="1" />
        <arg name="point0_x" value="15" />
        <arg name="point0_y" value="0" />
        <arg name="point0_z" value="1" />
        <arg name="point1_x" value="0.0" />
        <arg name="point1_y" value="0.0" />
        <arg name="point1_z" value="1.0" />
        <arg name="point2_x" value="15.0" />
        <arg name="point2_y" value="0.0" />
        <arg name="point2_z" value="1.0" />
        <arg name="point3_x" value="0.0" />
        <arg name="point3_y" value="0.0" />
        <arg name="point3_z" value="1.0" />
        <arg name="point4_x" value="15.0" />
        <arg name="point4_y" value="0.0" />
        <arg name="point4_z" value="1.0" />
```
出现问题，xml配置文件根据相应waypoints的个数修改了。
切换遥控器切换状态后，运行px4ctrl runctrl，再运行single_run_in_exp.launch和自动起飞后，

px4ctrlfsm打印：
AUTO_TAKEOFFF->AUTO_HOVER.

然后ego_replan_fsm打印:
[FSM]:state:WAIT_TARGET
wait for goal or trigger.

飞机大概处于悬停状态10S后，就突然往天上蹿。请问下这个怎么解决？

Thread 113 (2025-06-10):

Use D435i with Coolpi 4B(RK3588) problem

tom-jerr, 2025-06-10:
We are currently trying to compile and use librealsense from source on a CoolPi 4B(RK3588) to support our Intel RealSense D435i camera.

Our progress so far is as follows:
- We have successfully compiled the library on our system.
- The RGB Camera and Depth Camera functionalities are working correctly, and we can stream data from them without issues.

However, we are facing a problem: we are unable to receive the dual infrared (grayscale) image streams from the stereo cameras.
We understand that enabling these streams typically requires applying Intel's kernel patches to the system. The challenge is that our CoolPi 4B runs on a 5.10 kernel, and the official librealsense patches do not seem to support this version.

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

According the document, we have now recompiled librealsense on our CoolPi 4B (Kernel 5.10) with the -DFORCE_RSUSB_BACKEND=ON flag in CMake, as recommended. The goal was to bypass the kernel's uvcvideo driver, which does not recognize the RealSense camera's custom video formats.
However, after recompiling and attempting to run our application (or realsense-viewer), we can not read gray image from /camera/infra1 and /camera/infra2. Some useful messages list below.

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

How can we solve this problem? Please give us some advice.
Thank you for your help.

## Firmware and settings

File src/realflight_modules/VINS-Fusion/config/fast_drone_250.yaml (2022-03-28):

%YAML:1.0

#common parameters
#support: 1 imu 1 cam; 1 imu 2 cam: 2 cam; 
imu: 1         
num_of_cam: 2


imu_topic: "/mavros/imu/data_raw"
image0_topic: "/camera/infra1/image_rect_raw"
image1_topic: "/camera/infra2/image_rect_raw"




output_path: "/home/fast-drone/vins_output"


cam0_calib: "left.yaml"
cam1_calib: "right.yaml"
image_width: 640
image_height: 480
   

# Extrinsic parameter between IMU and Camera.
estimate_extrinsic: 1   # 0  Have an accurate extrinsic parameters. We will trust the following imu^R_cam, imu^T_cam, don't change it.
                        # 1  Have an initial guess about extrinsic parameters. We will optimize around your initial guess.

body_T_cam0: !!opencv-matrix
   rows: 4
   cols: 4
   dt: d
   data: [ -3.0597105734350372e-02, -5.8927835241672222e-03,
       9.9951442822153314e-01, 4.7302157421591003e-02,
       -9.9953144626651957e-01, -6.5966180705800959e-04,
       -3.0601515822914926e-02, 2.2936545354189812e-02,
       8.3966960215681175e-04, -9.9998241981978753e-01,
       -5.8698386963871307e-03, 6.1639590858913150e-02, 0., 0., 0., 1. ]
body_T_cam1: !!opencv-matrix
   rows: 4
   cols: 4
   dt: d
   data: [ -3.0069515759978405e-02, -5.7183785193312686e-03,
       9.9953145241611574e-01, 4.4848038940723180e-02,
       -9.9954744323873768e-01, -6.8446400583832556e-04,
       -3.0073912680706305e-02, -2.7107742793766636e-02,
       8.5611731814771996e-04, -9.9998341569054738e-01,
       -5.6952091272581828e-03, 6.1794907739113121e-02, 0., 0., 0., 1. ]
#Multiple thread support
multiple_thread: 1

#feature traker paprameters
max_cnt: 150            # max feature number in feature tracking
min_dist: 30            # min distance between two features 
freq: 10                # frequence (Hz) of publish tracking result. At least 10Hz for good estimation. If set 0, the frequence will be same as raw image 
F_threshold: 1.0        # ransac threshold (pixel)
show_track: 1           # publish tracking image as topic
flow_back: 1            # perform forward and backward optical flow to improve feature tracking accuracy

#optimization parameters
max_solver_time: 0.04  # max solver itration time (ms), to guarantee real time
max_num_iterations: 8   # max solver itrations, to guarantee real time
keyframe_parallax: 10.0 # keyframe selection threshold (pixel)

#imu parameters       The more accurate parameters you provide, the better performance
acc_n: 0.1          # accelerometer measurement noise standard deviation. #0.2   0.04
gyr_n: 0.01         # gyroscope measurement noise standard deviation.     #0.05  0.004
acc_w: 0.001         # accelerometer bias random work noise standard deviation.  #0.002
gyr_w: 0.0001       # gyroscope bias random work noise standard deviation.     #4.0e-5
g_norm: 9.805         # gravity magnitude

#unsynchronization parameters
estimate_td: 1                      # online estimate time offset between camera and imu
td: -0.05                             # initial value of time offset. unit: s. readed image clock + td = real image clock (IMU clock)

#loop closure parameters
load_previous_pose_graph: 0        # load and reuse previous pose graph; load from 'pose_graph_save_path'
pose_graph_save_path: "/home/fast/savedfiles/output/pose_graph/" # save and load path
save_image: 1                   # save image in pose graph for visualization prupose; you can close this function by setting 0 

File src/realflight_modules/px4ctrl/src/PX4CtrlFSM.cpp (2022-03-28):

#include "PX4CtrlFSM.h"
#include <uav_utils/converters.h>

using namespace std;
using namespace uav_utils;

PX4CtrlFSM::PX4CtrlFSM(Parameter_t &param_, LinearControl &controller_) : param(param_), controller(controller_) /*, thrust_curve(thrust_curve_)*/
{
	state = MANUAL_CTRL;
	hover_pose.setZero();
}

/* 
        Finite State Machine

	      system start
	            |
	            |
	            v
	----- > MANUAL_CTRL <-----------------
	|         ^   |    \                 |
	|         |   |     \                |
	|         |   |      > AUTO_TAKEOFF  |
	|         |   |        /             |
	|         |   |       /              |
	|         |   |      /               |
	|         |   v     /                |
	|       AUTO_HOVER <                 |
	|         ^   |  \  \                |
	|         |   |   \  \               |
	|         |	  |    > AUTO_LAND -------
	|         |   |
	|         |   v
	-------- CMD_CTRL

*/

void PX4CtrlFSM::process()
{

	ros::Time now_time = ros::Time::now();
	Controller_Output_t u;
	Desired_State_t des(odom_data);
	bool rotor_low_speed_during_land = false;

	// STEP1: state machine runs
	switch (state)
	{
	case MANUAL_CTRL:
	{
		if (rc_data.enter_hover_mode) // Try to jump to AUTO_HOVER
		{
			if (!odom_is_received(now_time))
			{
				ROS_ERROR("[px4ctrl] Reject AUTO_HOVER(L2). No odom!");
				break;
			}
			if (cmd_is_received(now_time))
			{
				ROS_ERROR("[px4ctrl] Reject AUTO_HOVER(L2). You are sending commands before toggling into AUTO_HOVER, which is not allowed. Stop sending commands now!");
				break;
			}
			if (odom_data.v.norm() > 3.0)
			{
				ROS_ERROR("[px4ctrl] Reject AUTO_HOVER(L2). Odom_Vel=%fm/s, which seems that the locolization module goes wrong!", odom_data.v.norm());
				break;
			}

			state = AUTO_HOVER;
			controller.resetThrustMapping();
			set_hov_with_odom();
			toggle_offboard_mode(true);

			ROS_INFO("\033[32m[px4ctrl] MANUAL_CTRL(L1) --> AUTO_HOVER(L2)\033[32m");
		}
		else if (param.takeoff_land.enable && takeoff_land_data.triggered && takeoff_land_data.takeoff_land_cmd == quadrotor_msgs::TakeoffLand::TAKEOFF) // Try to jump to AUTO_TAKEOFF
		{
			if (!odom_is_received(now_time))
			{
				ROS_ERROR("[px4ctrl] Reject AUTO_TAKEOFF. No odom!");
				break;
			}
			if (cmd_is_received(now_time))
			{
				ROS_ERROR("[px4ctrl] Reject AUTO_TAKEOFF. You are sending commands before toggling into AUTO_TAKEOFF, which is not allowed. Stop sending commands now!");
				break;
			}
			if (odom_data.v.norm() > 0.1)
			{
				ROS_ERROR("[px4ctrl] Reject AUTO_TAKEOFF. Odom_Vel=%fm/s, non-static takeoff is not allowed!", odom_data.v.norm());
				break;
			}
			if (!get_landed())
			{
				ROS_ERROR("[px4ctrl] Reject AUTO_TAKEOFF. land detector says that the drone is not landed now!");
				break;
			}
			if (rc_is_received(now_time)) // Check this only if RC is connected.
			{
				if (!rc_data.is_hover_mode || !rc_data.is_command_mode || !rc_data.check_centered())
				{
					ROS_ERROR("[px4ctrl] Reject AUTO_TAKEOFF. If you have your RC connected, keep its switches at \"auto hover\" and \"command control\" states, and all sticks at the center, then takeoff again.");
					while (ros::ok())
					{
						ros::Duration(0.01).sleep();
						ros::spinOnce();
						if (rc_data.is_hover_mode && rc_data.is_command_mode && rc_data.check_centered())
						{
							ROS_INFO("\033[32m[px4ctrl] OK, you can takeoff again.\033[32m");
							break;
						}
					}
					break;
				}
			}

			state = AUTO_TAKEOFF;
			controller.resetThrustMapping();
			set_start_pose_for_takeoff_land(odom_data);
			toggle_offboard_mode(true);				  // toggle on offboard before arm
			for (int i = 0; i < 10 && ros::ok(); ++i) // wait for 0.1 seconds to allow mode change by FMU // mark
			{
				ros::Duration(0.01).sleep();
				ros::spinOnce();
			}
			if (param.takeoff_land.enable_auto_arm)
			{
				toggle_arm_disarm(true);
			}
			takeoff_land.toggle_takeoff_land_time = now_time;

			ROS_INFO("\033[32m[px4ctrl] MANUAL_CTRL(L1) --> AUTO_TAKEOFF\033[32m");
		}

		if (rc_data.toggle_reboot) // Try to reboot. EKF2 based PX4 FCU requires reboot when its state estimator goes wrong.
		{
			if (state_data.current_state.armed)
			{
				ROS_ERROR("[px4ctrl] Reject reboot! Disarm the drone first!");
				break;
			}
			reboot_FCU();
		}

		break;
	}

	case AUTO_HOVER:
	{
		if (!rc_data.is_hover_mode || !odom_is_received(now_time))
		{
			state = MANUAL_CTRL;
			toggle_offboard_mode(false);

			ROS_WARN("[px4ctrl] AUTO_HOVER(L2) --> MANUAL_CTRL(L1)");
		}
		else if (rc_data.is_command_mode && cmd_is_received(now_time))
		{
			if (state_data.current_state.mode == "OFFBOARD")
			{
				state = CMD_CTRL;
				des = get_cmd_des();
				ROS_INFO("\033[32m[px4ctrl] AUTO_HOVER(L2) --> CMD_CTRL(L3)\033[32m");
			}
		}
		else if (takeoff_land_data.triggered && takeoff_land_data.takeoff_land_cmd == quadrotor_msgs::TakeoffLand::LAND)
		{

			state = AUTO_LAND;
			set_start_pose_for_takeoff_land(odom_data);

			ROS_INFO("\033[32m[px4ctrl] AUTO_HOVER(L2) --> AUTO_LAND\033[32m");
		}
		else
		{
			set_hov_with_rc();
			des = get_hover_des();
			if ((rc_data.enter_command_mode) ||
				(takeoff_land.delay_trigger.first && now_time > takeoff_land.delay_trigger.second))
			{
				takeoff_land.delay_trigger.first = false;
				publish_trigger(odom_data.msg);
				ROS_INFO("\033[32m[px4ctrl] TRIGGER sent, allow user command.\033[32m");
			}

			// cout << "des.p=" << des.p.transpose() << endl;
		}

		break;
	}

	case CMD_CTRL:
	{
		if (!rc_data.is_hover_mode || !odom_is_received(now_time))
		{
			state = MANUAL_CTRL;
			toggle_offboard_mode(false);

			ROS_WARN("[px4ctrl] From CMD_CTRL(L3) to MANUAL_CTRL(L1)!");
		}
		else if (!rc_data.is_command_mode || !cmd_is_received(now_time))
		{
			state = AUTO_HOVER;
			set_hov_with_odom();
			des = get_hover_des();
			ROS_INFO("[px4ctrl] From CMD_CTRL(L3) to AUTO_HOVER(L2)!");
		}
		else
		{
			des = get_cmd_des();
		}

		if (takeoff_land_data.triggered && takeoff_land_data.takeoff_land_cmd == quadrotor_msgs::TakeoffLand::LAND)
		{
			ROS_ERROR("[px4ctrl] Reject AUTO_LAND, which must be triggered in AUTO_HOVER. \
					Stop sending control commands for longer than %fs to let px4ctrl return to AUTO_HOVER first.",
					  param.msg_timeout.cmd);
		}

		break;
	}

	case AUTO_TAKEOFF:
	{
		if ((now_time - takeoff_land.toggle_takeoff_land_time).toSec() < AutoTakeoffLand_t::MOTORS_SPEEDUP_TIME) // Wait for several seconds to warn prople.
		{
			des = get_rotor_speed_up_des(now_time);
		}
		else if (odom_data.p(2) >= (takeoff_land.start_pose(2) + param.takeoff_land.height)) // reach the desired height
		{
			state = AUTO_HOVER;
			set_hov_with_odom();
			ROS_INFO("\033[32m[px4ctrl] AUTO_TAKEOFF --> AUTO_HOVER(L2)\033[32m");

			takeoff_land.delay_trigger.first = true;
			takeoff_land.delay_trigger.second = now_time + ros::Duration(AutoTakeoffLand_t::DELAY_TRIGGER_TIME);
		}
		else
		{
			des = get_takeoff_land_des(param.takeoff_land.speed);
		}

		break;
	}
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

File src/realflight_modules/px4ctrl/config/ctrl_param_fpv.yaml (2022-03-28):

#########################################################################
# ⭐⭐⭐  Set parameters carefully for satisfied performance!   ⭐⭐⭐ #
#########################################################################

mass        : 1.2 # kg 
gra         : 9.81 
pose_solver : 1     # 0:From ZhepeiWang (drag & less singular) 1:From ZhepeiWang, 2:From rotor-drag    
ctrl_freq_max   : 100.0
use_bodyrate_ctrl: false
max_manual_vel: 1.0
max_angle: 30  # Attitude angle limit in degree. A negative value means no limit.
low_voltage: 13.2 # 4S battery

rc_reverse: # *
    roll: false
    pitch: false
    yaw: false
    throttle: false

auto_takeoff_land:
    enable: true
    enable_auto_arm: true
    no_RC: false
    takeoff_height: 1.0 # m
    takeoff_land_speed: 0.3 # m/s

thrust_model: # The model that maps thrust signal u(0~1) to real thrust force F(Unit:N): F=K1*Voltage^K2*(K3*u^2+(1-K3)*u). 
    print_value: false # display the value of “thr_scale_compensate” or “hover_percentage” during thrust model estimating.
    accurate_thrust_model: false  # This can always enabled if don't require accurate control performance :-)
    # accurate thrust mapping parameters
    K1: 0.7583 # Needs precise calibration!
    K2: 1.6942 # Needs precise calibration!
    K3: 0.6786 # Needs precise calibration! K3 equals THR_MDL_FAC in https://docs.px4.io/master/en/config_mc/pid_tuning_guide_multicopter.html.
    # approximate thrust mapping parameters
    hover_percentage: 0.30  # Thrust percentage in Stabilize/Arco mode # *

gain: 
    # Cascade PID controller. Recommend to read the code.
    Kp0: 1.5
    Kp1: 1.5 
    Kp2: 1.5
    Kv0: 1.5
    Kv1: 1.5
    Kv2: 1.5
    # ↓↓↓ No use now --
    Kvi0: 0.0
    Kvi1: 0.0
    Kvi2: 0.0
    Kvd0: 0.0
    Kvd1: 0.0
    Kvd2: 0.0
    # ↓↓↓ Only used in rate control mode.
    KAngR: 20.0
    KAngP: 20.0
    KAngY: 20.0

rotor_drag:  
    x: 0.0  # The reduced acceleration on each axis caused by rotor drag. Unit:(m*s^-2)/(m*s^-1).
    y: 0.0  # Same as above
    z: 0.0  # Same as above
    k_thrust_horz: 0.0 # Set to 0 recommended... --

msg_timeout:
    odom: 0.5
    rc:   0.5
    cmd:  0.5
    imu:  0.5
    bat:  0.5

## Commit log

2022-03-29 update purchase list
    [purchase_list.xlsx]
2022-03-30 update chapter 8
    [purchase_list.xlsx]
2022-10-14 fix some bugs in readme
    [purchase_list.xlsx]
2022-10-18 add v5+ version carbon board
    [底板 加长.STEP, 顶板 加长.STEP]
2022-10-24 fix bugs
    [底板 加长.STEP]
2022-11-09 remove v5 carbon board
    [底板 加长.STEP, 顶板 加长.STEP]
